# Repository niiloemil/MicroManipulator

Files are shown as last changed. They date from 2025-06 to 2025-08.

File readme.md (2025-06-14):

# 3D-Printed Flexure Micro-Manipulator
This project contains am open source low-cost, easy-to-build **XYZ Micro-Manipulator** platform. 

It's designed for applications such as optical alignment, probing electronic components, and microscopy.
Thanks to its parallel kinematic structure and integrated flexures, it achieves good mechanical stiffness for a 3D-printed device, as well as micrometer precision.

<div style="display: flex;">
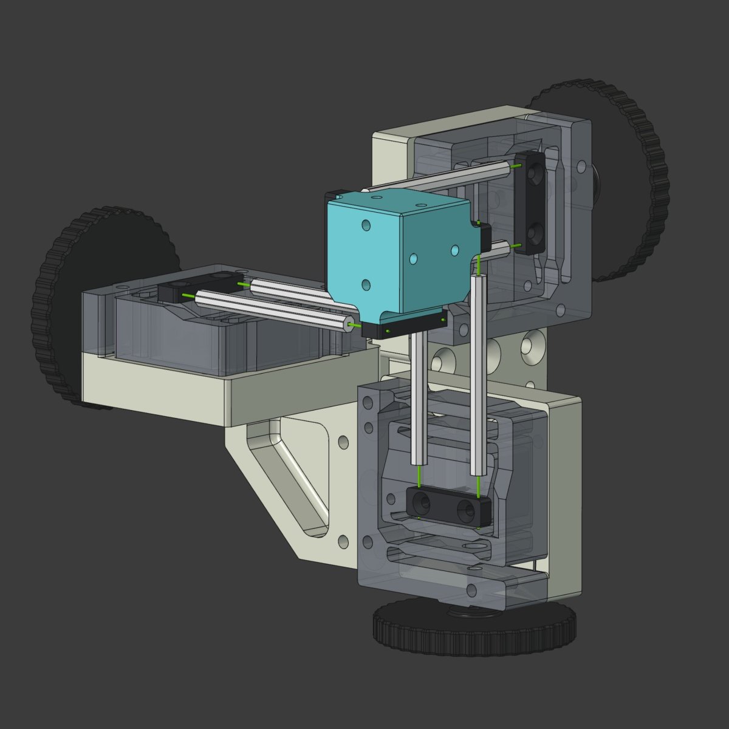
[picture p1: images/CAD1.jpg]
    
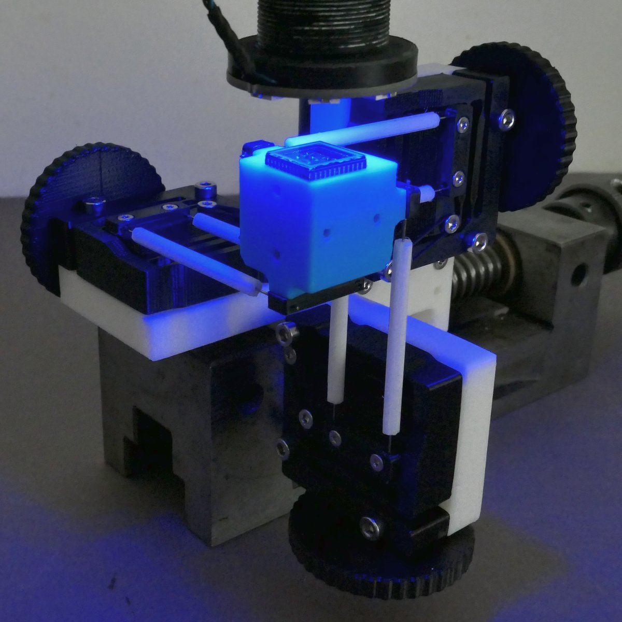
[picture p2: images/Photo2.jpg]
    
</div>

The design was partially inspired by another great open source flexure stage 'The OpenFlexure Block Stage - Sub-100 nm fibre alignment with a monolithic plastic flexure stage' 

### ✨ Examples

Below you find some examples of the translation stage in action. But there are many more possible use cases to be discovered...

<div style="display: flex;">
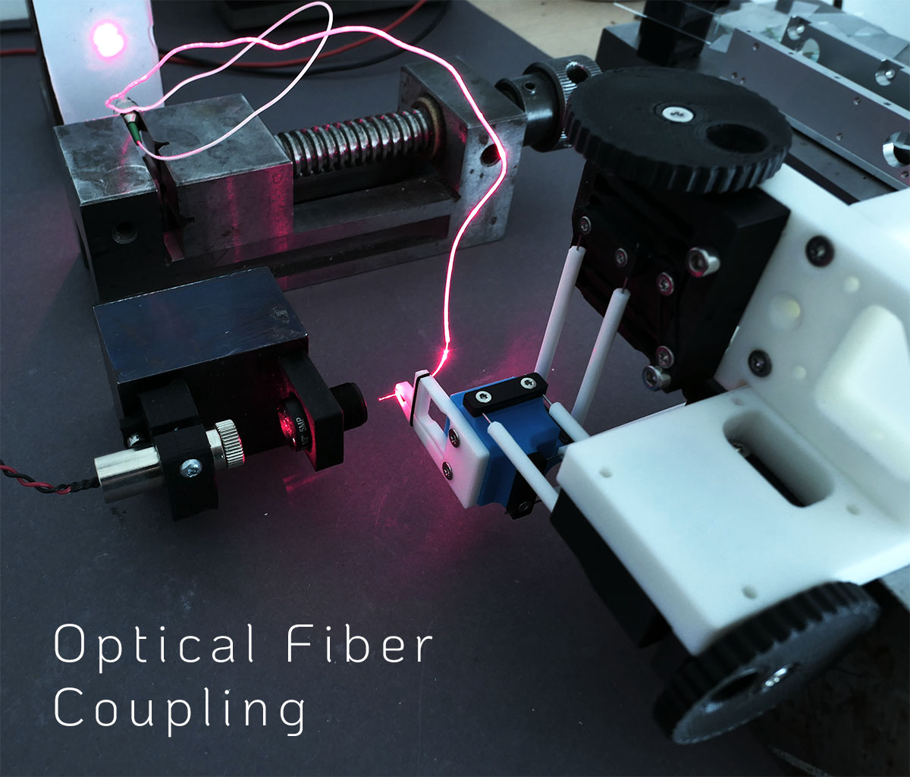
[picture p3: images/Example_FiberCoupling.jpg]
Example 1
    
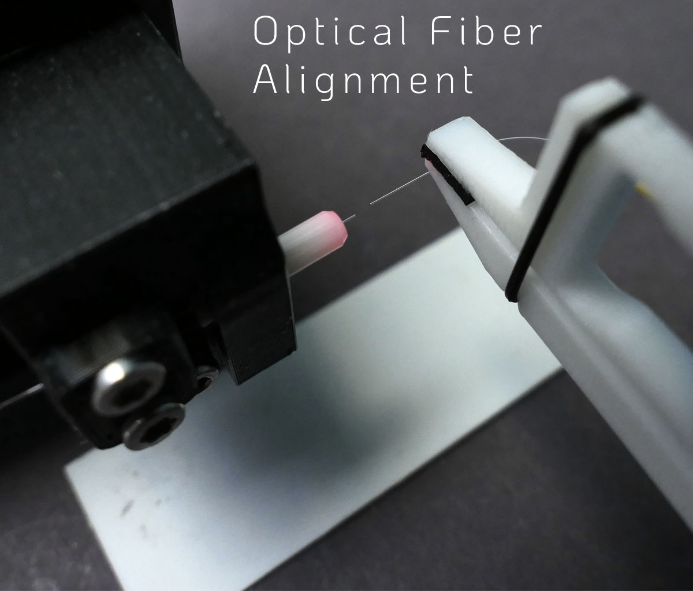
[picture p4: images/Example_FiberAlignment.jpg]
Example 2
    
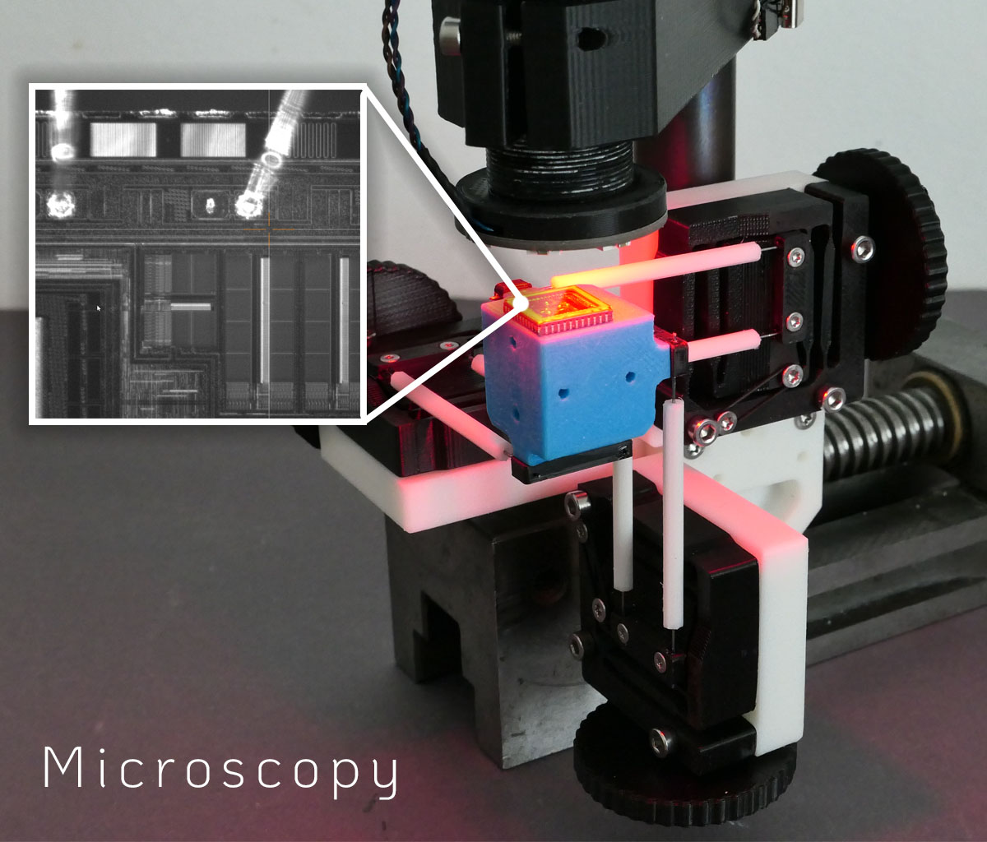
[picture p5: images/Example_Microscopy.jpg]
Example 3
    
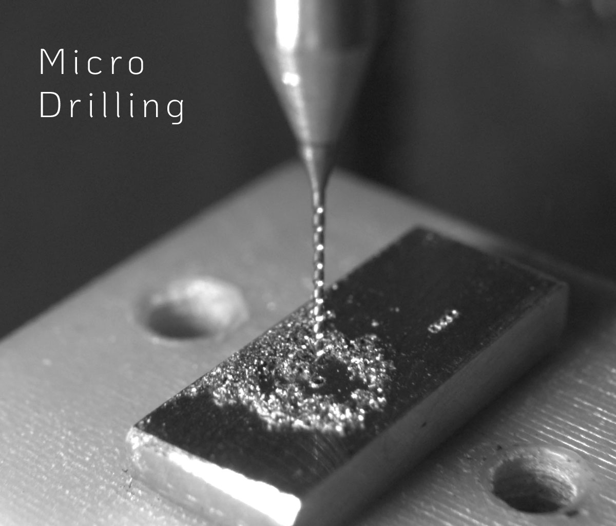
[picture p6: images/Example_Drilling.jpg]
Example 3
    
</div>

<br><br>

### ⚙ CAD-Files

All CAD models are made in FreeCAD, to allow everyone to view and modify the design without subscribing or paying for a propriatary CAD solution.

<div style="display: flex;">
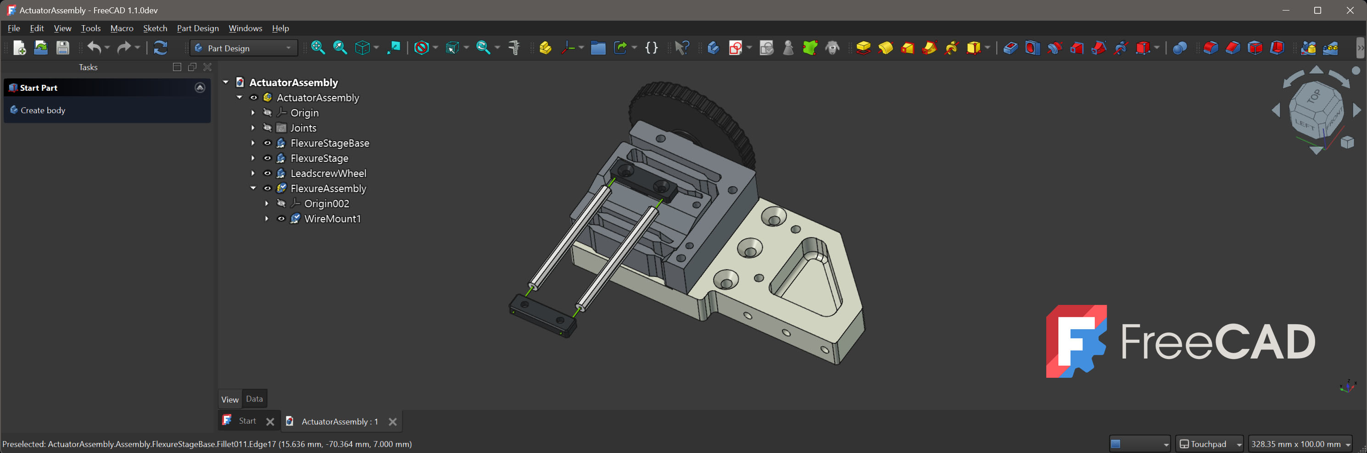
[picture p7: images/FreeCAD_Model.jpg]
FreeCAD Model
    
</div>

<br>

The files for the metric version can be found here: [CAD Models Metric](construction_metric).
Please note that FreeCAD version **1.1.0dev** was used and the files might not work with older versions.

### ✅ 3D-Printing

Ready to print 3d-models are here: [Files for 3D-Printing](print_files/v2).

<div style="display: flex;">
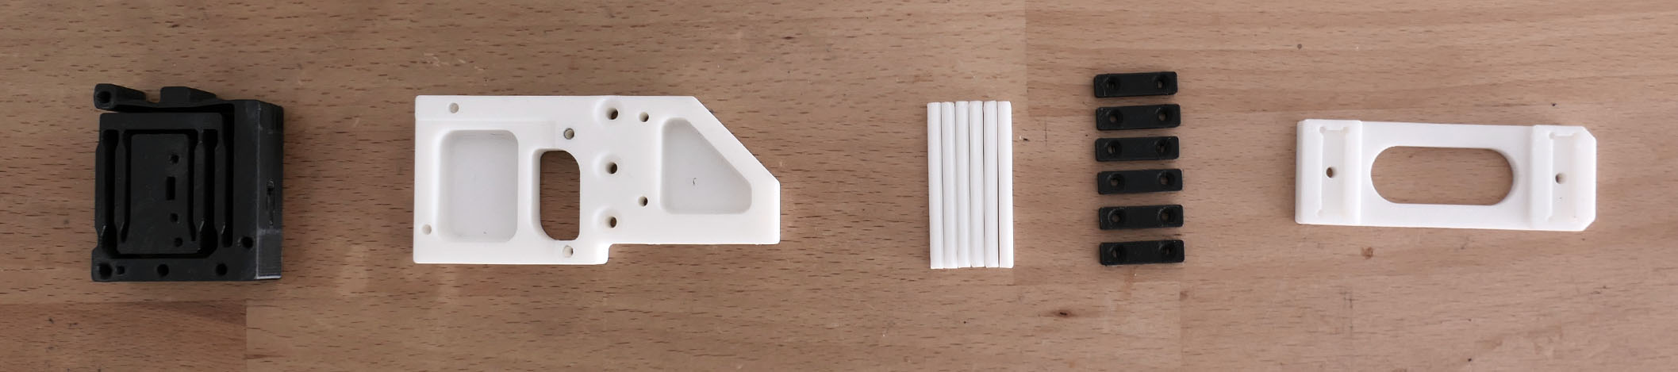
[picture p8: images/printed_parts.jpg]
    
</div>

Parts are optimized for 0.4mm print nozzle and PLA. The parts 'WireMount' and 'FlexureStiffener' should be printed at slow speed (25mm/s) and with 0.1mm layerheight to ensure good quality prints.
All other parts can be printed with 0.2mm or 0.25mm layer height and regular speed. The endeffector requires a little bit of support, which is easy to peel of for this simple geometry.

### 📄Resources

Here are some great resources and similar projects from which inspiration for this project was drawn.

* [Open Flexure Microscope](https://openflexure.org/projects/microscope/)
* [The OpenFlexure Block Stage](https://arxiv.org/abs/1911.09986).

### 🚀 Contribute 

There are some open task for everyone wanting to contribute to this project:

* Create CAD model for imperial units.
* Improve O-Ring Flexure preload mechanism.
* Find an easy way to mount the crank wheels true and without 'wobble' to M3 bolts.
* Create useful endeffector attachments and grippers.

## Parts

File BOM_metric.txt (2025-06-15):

*** HARDWARE **********************************************

Qty   Name                              Dimensions
----  --------------------------------  -------------------
3     Countersunk Screw                 M3 x 30mm
18    Countersunk Screw                 M3 x 18mm
12    Countersunk Screw (Trox)          M2 x 8mm
12    Countersunk Screw (Trox)          M2 x 8mm
12    Countersunk Screw (Trox)          M2.5 x 6mm
6     O-Ring (Silicone / Viton)         ID=6mm, CS=1mm
3     Washer                            M3
1m    Piano wire / Spring steel rod     D=0.5mm
1     CA-Glue / Superglue               1g

*** 3D-PRINTED PARTS **************************************

Qty   Name                              
---   -----------------------------------------------------
6     WireMount
6     FlexureStiffener
3     FlexureStage
3     FlexureStageBase
3     LeadscrewWheel
1     EndEffector
1     WireMountFixture

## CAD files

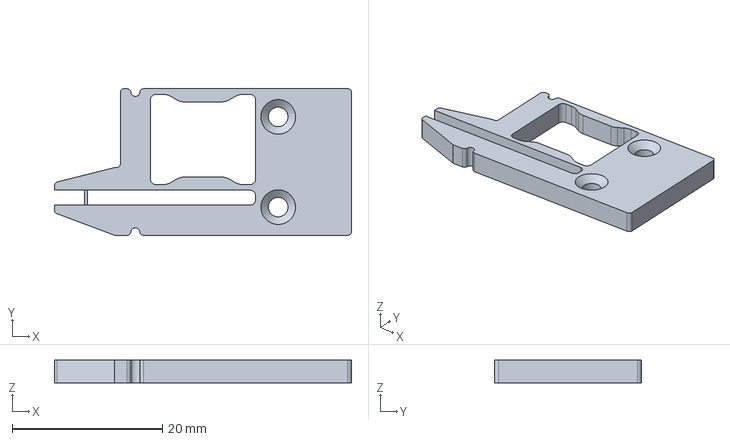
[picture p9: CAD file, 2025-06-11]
construction_metric/attachments/Gripper1.FCStd
39.5 x 19.5 x 3.00 mm

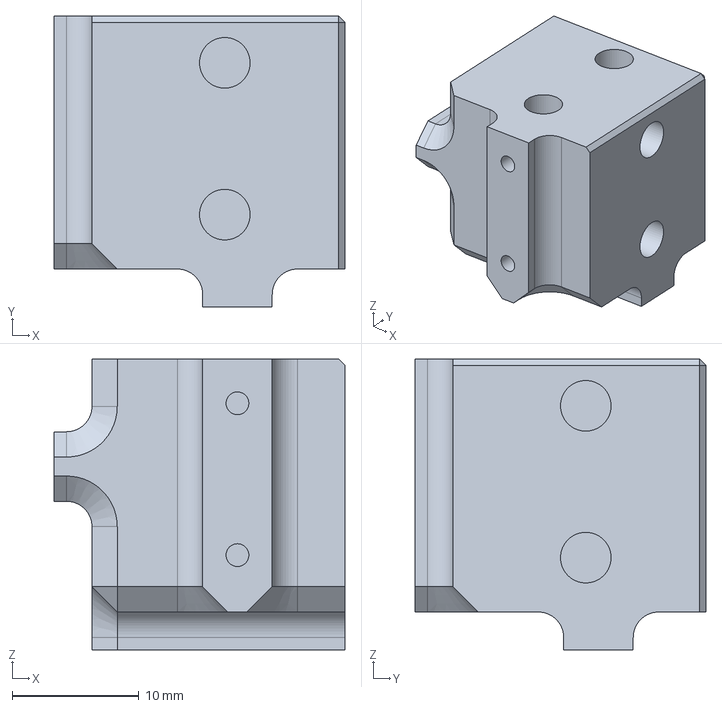
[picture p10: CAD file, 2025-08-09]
construction_metric/v2_variation1/EndEffector-M3-inserts.FCStd
23.0 x 23.0 x 23.0 mm

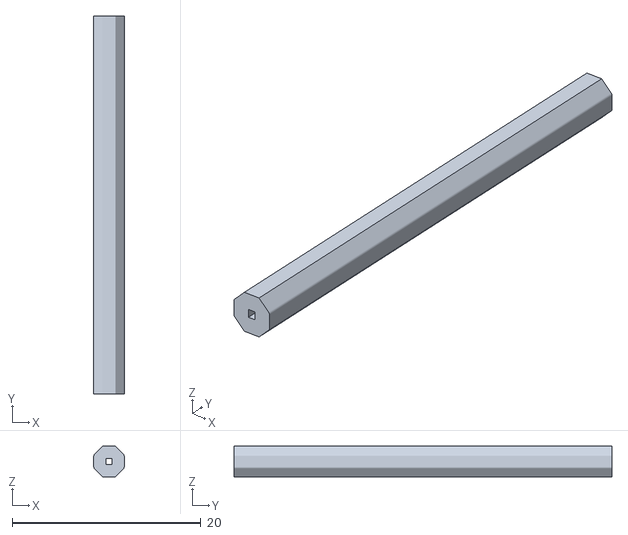
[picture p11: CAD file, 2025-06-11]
print_files/v2/FlexureStiffener.obj
3.23 x 40.0 x 3.23

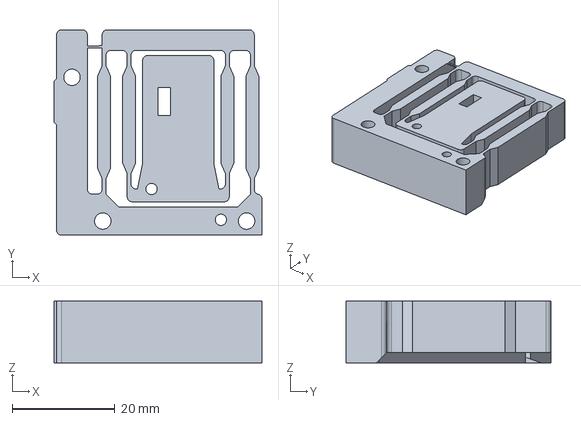
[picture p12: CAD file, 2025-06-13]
construction_metric/v2/FlexureStage.FCStd
40.5 x 40.0 x 12.0 mm

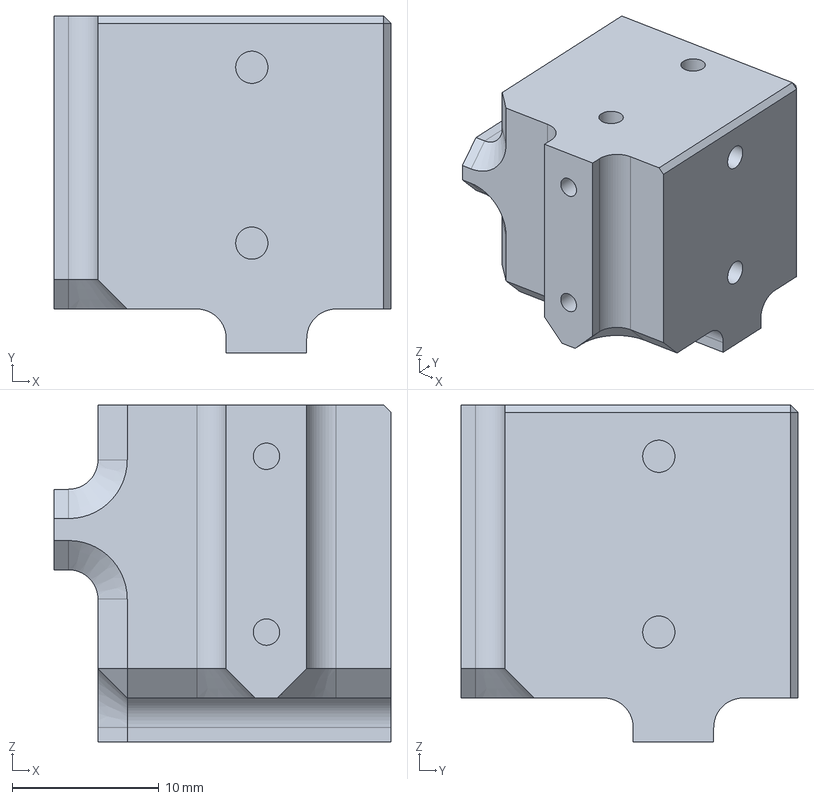
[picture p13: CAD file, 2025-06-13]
construction_metric/v2/EndEffector.FCStd
23.0 x 23.0 x 23.0 mm

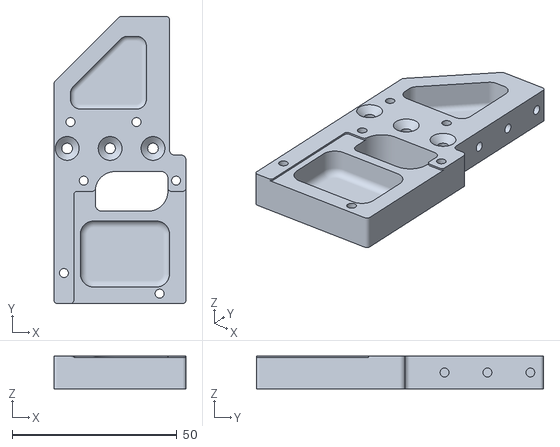
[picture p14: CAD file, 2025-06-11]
print_files/v2/FlexureStageBase.obj
40.0 x 87.0 x 10.0

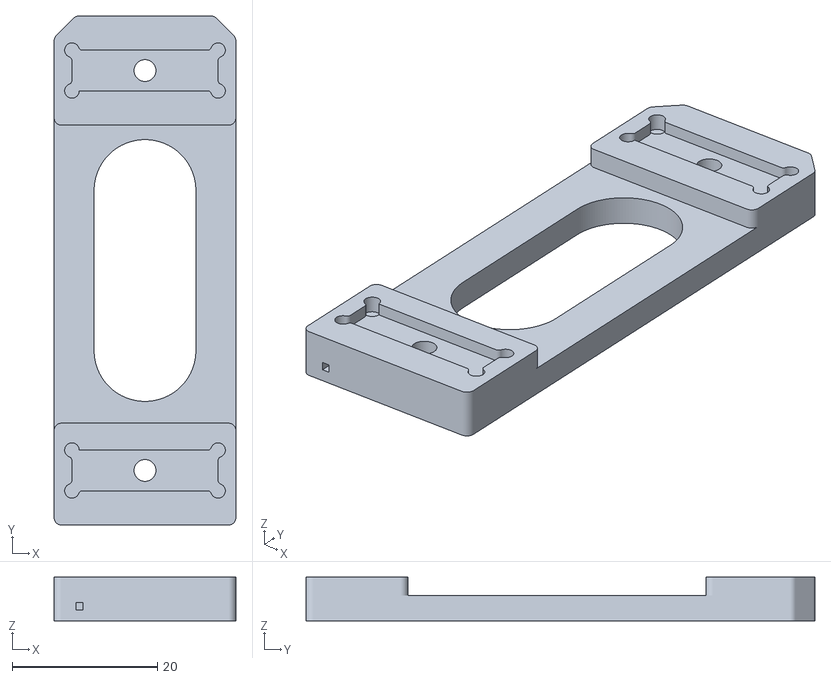
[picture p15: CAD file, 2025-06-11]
print_files/v2/WireMountFixture.obj
25.0 x 70.0 x 6.00

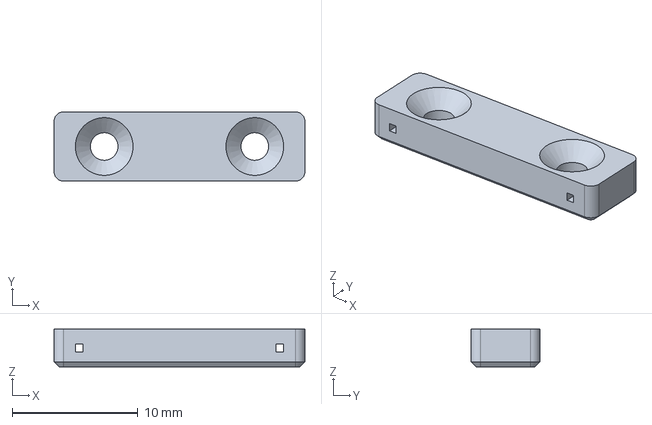
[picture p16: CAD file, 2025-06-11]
construction_metric/v2/WireMount.FCStd
20.0 x 5.50 x 3.00 mm

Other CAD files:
construction_metric/v2/ActuatorAssembly.FCStd
construction_metric/v2/MicroManipulatorAssembly.FCStd
construction_metric/v2/EndEffectorAssembly.FCStd
construction_metric/v2/FlexureAssembly.FCStd
construction_metric/attachments_variation1/Gripper1-M3-clearance.FCStd
print_files/v2_variation1/EndEffector-M3-inserts.obj
print_files/v2/FlexureStage.obj
print_files/v2/EndEffector.obj
print_files/v2/WireMount.obj
construction_metric/v2/WireMountFixture.FCStd
construction_metric/v2/FlexureStageBase.FCStd
construction_metric/v2/FlexureStageBase_Column.FCStd
construction_metric/v2/FlexureStiffener.FCStd
construction_metric/v2/FlexureWire.FCStd
construction_metric/v2/LeadscrewWheel.FCStd
print_files/v2/LeadscrewWheel.obj

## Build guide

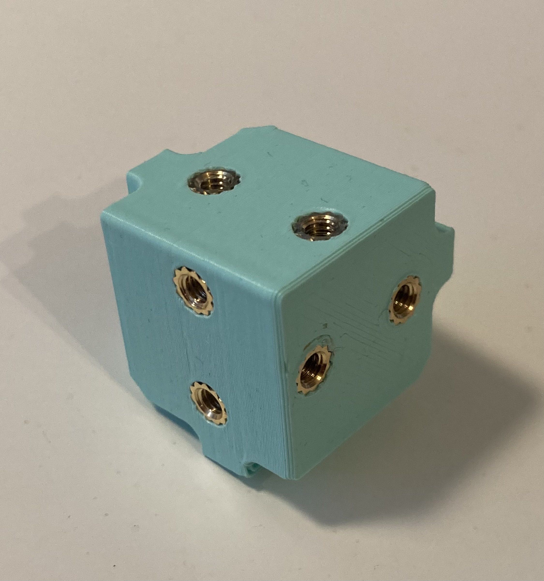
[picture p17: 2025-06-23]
print_files/v2_variation1/EndEffector-M3-inserts.jpg

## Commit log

2025-06-11 print files
    [EndEffector.obj, FlexureStage.obj, FlexureStageBase.obj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]
2025-06-13 CAD model fix
    [ActuatorAssembly.FCStd, EndEffector.FCStd, EndEffectorAssembly.FCStd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]
2025-06-13 minor changes
    [ActuatorAssembly.FCStd, FlexureStage.FCStd]
2025-06-23 Create alternate CAD folder
2025-06-23 Image of EE with threaded inserts
2025-08-09 restructured and added CAD files
    [EndEffector-M3-inserts.FCStd, EndEffector-M3-inserts.obj, Gripper1-M3-clearance.FCStd]
